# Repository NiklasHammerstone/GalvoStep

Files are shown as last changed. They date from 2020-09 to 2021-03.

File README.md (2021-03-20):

# GalvoStep
Project for building a cheap galvo laser system using Stepper motors and widely available parts.
The main goal is to engrave pictures onto wood much faster than a XY-machine could. 

This repo contains mechanical and electrical diagrams, firmware and extensive documentation of this project to maximize accessibility.
Feel free to copy/advance this project.

For a documentation of the supported G-code commands see the wiki.

### Final Update 20.03.2021

GalvoStep V1 is finished. See https://youtu.be/tV-LJvpVcUo for a typical engraving process. Accuracy is +-0.5mm I'd say. All the software can be found in CODES. 

### UPDATE 04.01.2021:
GalvoStep V1 is now functional but requires further testing. See https://youtu.be/xkFyk6ncNaY for initial test.
GUI (.py and .exe) and the Firmware for Teensy 4.0 can be found in CODES
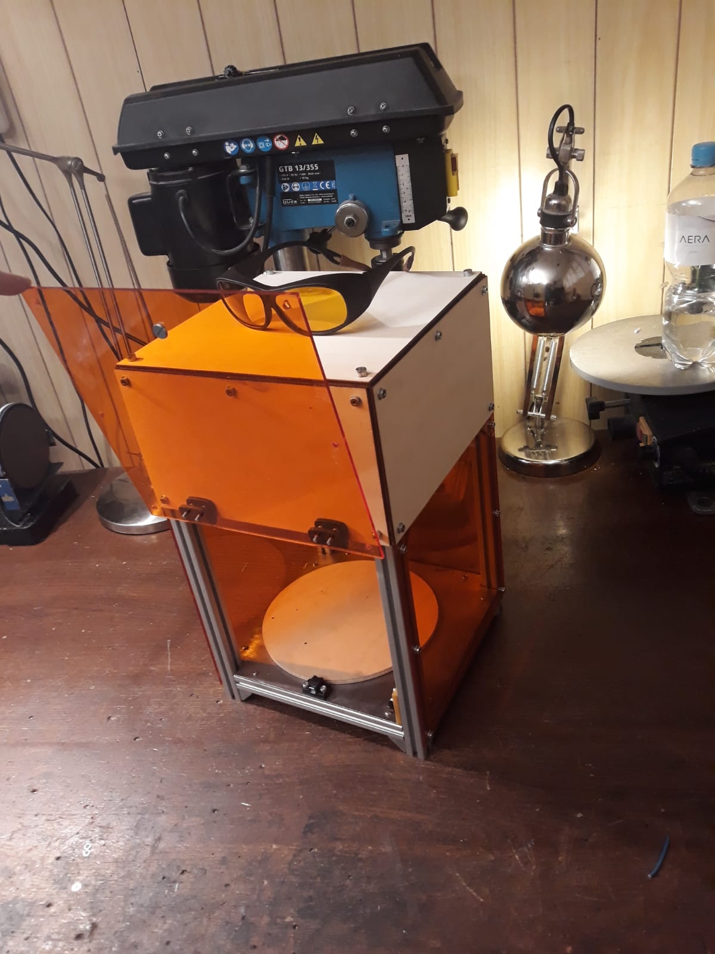
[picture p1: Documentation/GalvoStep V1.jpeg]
Most recent picture of GalvoStepV1

### UPDATE 11.10.2020:
The prototype report is done. See Documentation. GalvoStep V0 (proof-of-concept) is finished.
Now onto V1! (Goal: Actually engraving pictures)
### UPDATE 01.10.2020:
First prototype is now functional!
https://www.youtube.com/watch?v=stV5wWasxEc

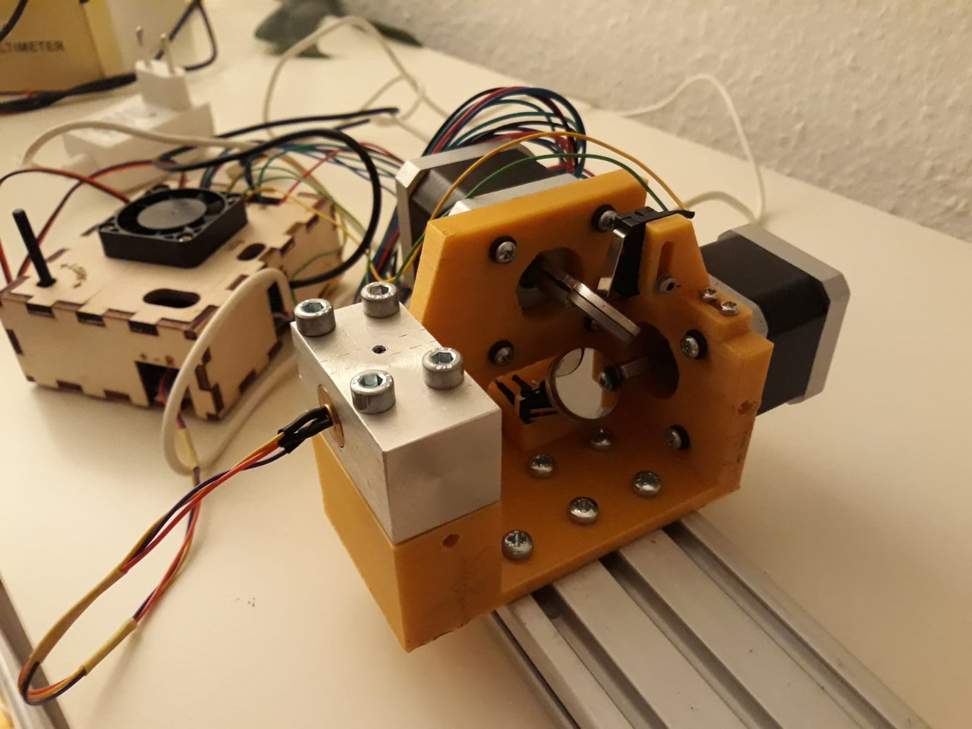
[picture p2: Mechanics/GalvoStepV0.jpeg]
Most recent picture of the prototype


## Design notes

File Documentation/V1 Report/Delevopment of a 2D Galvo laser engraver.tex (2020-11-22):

\documentclass[a4paper, 11pt]{scrartcl}
\usepackage[utf8]{inputenc}
\usepackage[english]{babel}
\usepackage[T1]{fontenc}
\usepackage{amsmath}
\usepackage{graphicx}
\usepackage{url}
\usepackage{float}
\usepackage{fancyhdr}
\bibliographystyle{plainnat}
\newcommand{\uproman}[1]{\uppercase\expandafter{\romannumeral#1}}

\title {Delevopment of a 2D Galvo laser engraver}
\author {Niklas H}
\date {\today}

\begin{document}
\maketitle
\tableofcontents
\newpage

\section{Introduction}
In this documentation, the construction of a Galvo-style high-speed laser engraver will be discussed. The goal is to upgrade the existing device to a user friendly laser engraver with high engraving speed.

\section{Theory}
In this section, relevant theory will be discussed. The development of the scanner will be based on these details. \\
\subsection{Laser diodes} 

\subsection{Stepper motors}

\subsection{Optics of the scanner} 

\section{Implementation}
In this section, construction details of the galvo scanner will be explained.
\subsection{Mechanics and Optics}
\begin{figure}[H]
\begin{center}
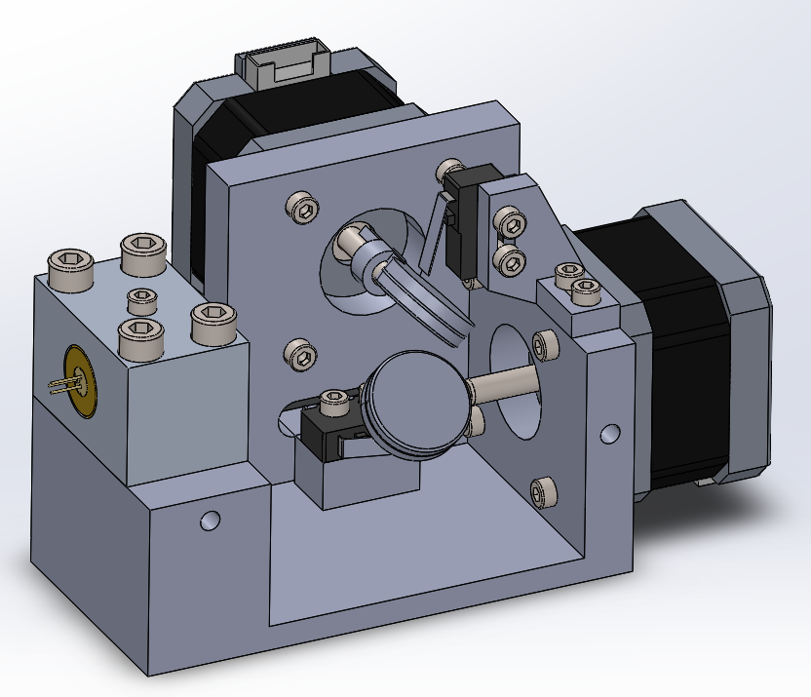
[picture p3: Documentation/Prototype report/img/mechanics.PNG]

\caption{CAD-Rendering of the mechanical system}
\label{mechanics}
\end{center}
\end{figure}

\addcontentsline{toc}{section}{References}
\bibliography{literature}
\end{document}

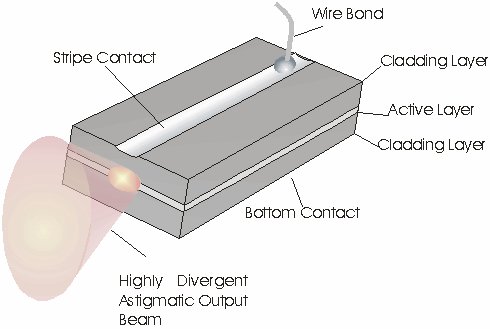
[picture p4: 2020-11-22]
Documentation/V1 Report/img/Beamshape.jpg

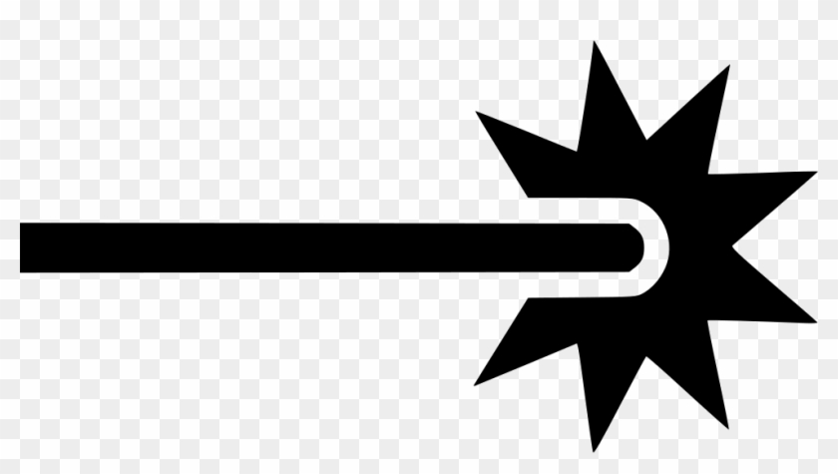
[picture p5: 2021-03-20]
Codes/lasersign.jpg

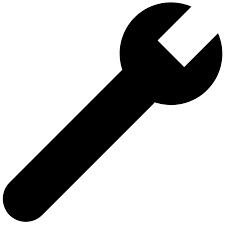
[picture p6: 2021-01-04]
Codes/wrench.png

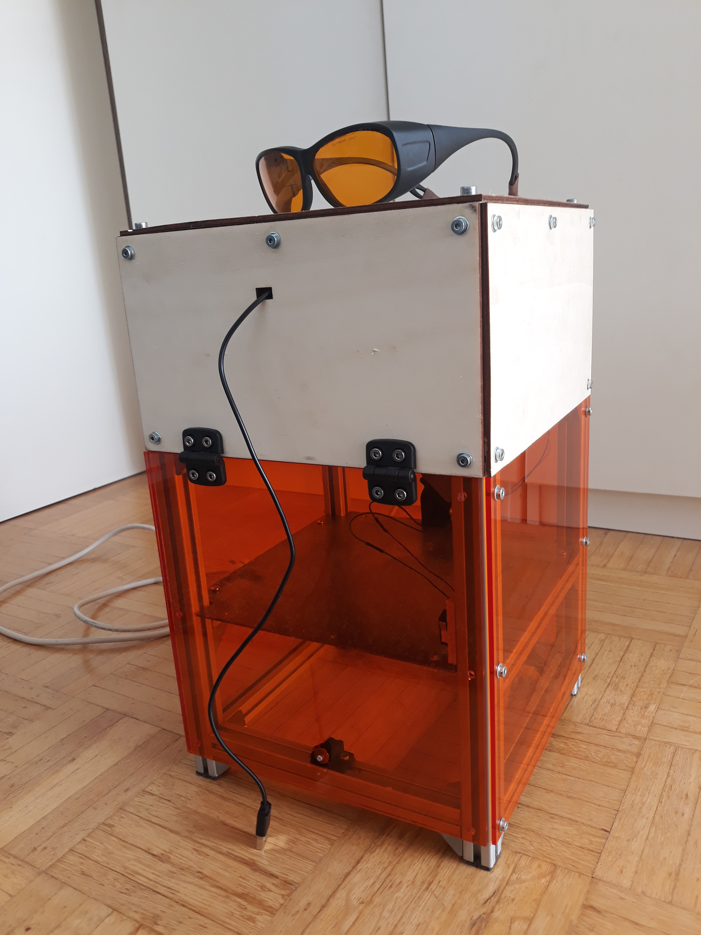
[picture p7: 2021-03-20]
Documentation/thumbnail.jpg

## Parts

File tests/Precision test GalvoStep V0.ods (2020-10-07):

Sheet: D231_F5000
 | D = 231 |  |  | F = 5000
 | TargetPosition | X | Position |  | TargetPosition | Y | Position | TargetPosition |  |  | Position
 |  |  |  |  |  |  |  | X | Y | X | Y
0 | -40 |  | -40 |  |  |  |  | 0 | 0 | 0 | 0
0 | -30 |  | -30.8 |  |  |  |  | 10 | 10 | 9.3 | 9.4
0 | -20 |  | -20.7 |  | -20 |  | -18.8 | 20 | 20 | 18.8 | 19.3
0 | -10 |  | -11.1 |  | -10 |  | -9.7 | 30 | 30 | 29.2 | 29.2
0 | 0 |  | 0 |  | 0 |  | 0 | 40 | 40 | 39.5 | 39.5
0 | 10 |  | 9 |  | 10 |  | 9.7 | 50 | 50 | 49.6 | 50
0 | 20 |  | 18.6 |  | 20 |  | 19.7 | 60 | 60 | 60.3 | 60.2
0 | 30 |  | 29.1 |  | 30 |  | 29.6 | 70 | 70
0 | 40 |  | 39.5 |  | 40 |  | 40
0 | 50 |  | 49.5 |  | 50 |  | 50
0 | 60 |  | 59.3 |  | 60 |  | 59.5
0 | 70 |  | 69.1 |  | 70 |  | 69.4
 |  |  |  |  | AVERAGE X DIFFERENCE: |  | -0.118452381 |  |  | SLOPE: | 0.999144016
 |  |  |  |  | AVERAGE Y DIFFERENCE: |  | 0.141428571 |  |  | INTERCEPT: | 0.153847409
 |  |  |  |  | MAX X DIFFERENCE: |  | 1.4
 |  |  |  |  | MAX Y DIFFERENCE: |  | 1.2

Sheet: D231_F2000
 | D = 231 |  |  | F = 2000
 | TargetPosition | X | Position |  | TargetPosition | Y | Position | TargetPosition |  |  | Position
 |  |  |  |  |  |  |  | X | Y | X | Y
0 | -40 |  | -39.5 |  |  |  |  | 0 | 0 | 0 | 0
0 | -30 |  | -29.7 |  | -30 |  | -28.7 | 10 | 10 | 9 | 10
0 | -20 |  | -19.8 |  | -20 |  | -18.6 | 20 | 20 | 18.7 | 20
0 | -10 |  | -10 |  | -10 |  | -8.5 | 30 | 30 | 29 | 30
0 | 0 |  | 0 |  | 0 |  | 0 | 40 | 40 | 39 | 40.6
0 | 5 |  | 3.8 |  | 5 |  | 5 | 50 | 50 | 49.3 | 50.7
0 | 10 |  | 8.8 |  | 10 |  | 10 | 60 | 60 | 59.1 | 61
0 | 20 |  | 18.3 |  | 20 |  | 20 | 70 | 70 | 69.5 | 71
0 | 30 |  | 28.7 |  | 30 |  | 30.3
0 | 40 |  | 38.4 |  | 40 |  | 40.6
0 | 50 |  | 48.7 |  | 50 |  | 51
0 | 60 |  | 58.6 |  | 60 |  | 60.8
0 | 70 |  | 69 |  | 70 |  | 71
0 | 80 |  | 78.6 |  | 80 |  | 81.5
 |  |  |  |  | AVERAGE X DIFFERENCE: |  | 0.003571429 |  |  | SLOPE: | 1.018746181
 |  |  |  |  | AVERAGE Y DIFFERENCE: |  | 0.155288462 |  |  | INTERCEPT: | 0.571380624
 |  |  |  |  | MAX X DIFFERENCE: |  | 1.7
 |  |  |  |  | MAX Y DIFFERENCE: |  | 1.5

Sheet: D150_F2000
 | D = 150 |  |  | F = 2000
 | TargetPosition | X | Position |  | TargetPosition | Y | Position | TargetPosition |  |  | Position
 |  |  |  |  |  |  |  | X | Y | X | Y
0 | -40 |  | -39.6 |  |  |  |  | 0 | 0 | 0 | 0
0 | -30 |  | -30.5 |  | -30 |  |  | 10 | 10 | 9 | 10
0 | -20 |  | -20 |  | -20 |  | -20.5 | 20 | 20 | 19.1 | 20
0 | -10 |  | -10 |  | -10 |  | -10 | 30 | 30 | 29.6 | 30
0 | 0 |  | 0 |  | 0 |  | 0 | 40 | 40 | 39.4 | 40
0 | 10 |  | 9.6 |  | 10 |  | 10 | 50 | 50 | 50.3 | 51
0 | 20 |  | 19.6 |  | 20 |  | 20 | 60 | 60 | 60.2 | 61.1
0 | 30 |  | 29.8 |  | 30 |  | 30.4 | 70 | 70 | 70.8 | 71.7
0 | 40 |  | 39.6 |  | 40 |  | 40.8
0 | 50 |  | 49.8 |  | 50 |  | 50.7
0 | 60 |  | 59.6 |  | 60 |  | 60.7
0 | 70 |  | 69.7 |  | 70 |  | 71.3
0 | 80 |  | 80.3 |  | 80
 |  |  |  |  | AVERAGE X DIFFERENCE: |  | 0.019230769 |  |  | SLOPE: | 1.006170769
 |  |  |  |  | AVERAGE Y DIFFERENCE: |  | -0.0675 |  |  | INTERCEPT: | 0.460257238
 |  |  |  |  | MAX X DIFFERENCE: |  | 1
 |  |  |  |  | MAX Y DIFFERENCE: |  | 1.7

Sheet: D150_F5000
 | D = 150 |  |  | F = 5000
 | TargetPosition | X | Position |  | TargetPosition | Y | Position | TargetPosition |  |  | Position
 |  |  |  |  |  |  |  | X | Y | X | Y
0 | -40 |  | -40 |  |  |  |  | 0 | 0 | 0 | 0
0 | -30 |  | -31 |  | -30 |  |  | 10 | 10 | 8.9 | 10.2
0 | -20 |  | -20.8 |  | -20 |  | -19.2 | 20 | 20 | 19.6 | 20.3
0 | -10 |  | -10.5 |  | -10 |  | -8.6 | 30 | 30 | 29.3 | 30.7
0 | 0 |  | 0 |  | 0 |  | 0 | 40 | 40 | 39.1 | 40.4
0 | 10 |  | 9.3 |  | 10 |  | 10.3 | 50 | 50 | 50 | 50.8
0 | 20 |  | 19.7 |  | 20 |  | 20.4 | 60 | 60 | 60.1 | 60.7
0 | 30 |  | 29.8 |  | 30 |  | 31 | 70 | 70
0 | 40 |  | 39.4 |  | 40 |  | 40.6
0 | 50 |  | 49.7 |  | 50 |  | 50.8
0 | 60 |  | 59.2 |  | 60 |  | 60.6
0 | 70 |  | 69.3 |  | 70 |  | 72
 |  |  |  |  | AVERAGE X DIFFERENCE: |  | -0.031547619 |  |  | SLOPE: | 1.004509858
 |  |  |  |  | AVERAGE Y DIFFERENCE: |  | 0.173571429 |  |  | INTERCEPT: | 0.738065618
 |  |  |  |  | MAX X DIFFERENCE: |  | 1.1
 |  |  |  |  | MAX Y DIFFERENCE: |  | 2
 |  |  |  |  |  |  |  |  |  |  | Trendline

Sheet: Sheet4
AVERAGE DIFFERENCE |  |  | AVERAGE DIFFERENCE
X | F2000 | F5000 | Y | F2000 | F5000
D150 | 0.019230769 | -0.031547619 | D150 | -0.0675 | 0.173571429
D231 | 0.003571429 | -0.118452381 | D231 | 0.155288462 | 0.141428571
MAXIMUM DIFFERENCE |  |  | MAXIMUM DIFFERENCE
X | F2000 | F5000 | Y | F2000 | F5000
D150 | 1 | 1.1 | D150 | 1.7 | 2
D231 | 1.7 | 1.4 | D231 | 1.5 | 1.2
SLOPE OF TRENDLINE (IDEAL LINEARITY: 1) |  |  | INTERCEPT OF TRENDLINE (IDEAL ACCURACY: 0)
 | F2000 | F5000 |  | F2000 | F5000
D150 | 1.006170769 | 1.004509858 | D150 | 0.460257238 | 0.738065618
D231 | 1.018746181 | 0.999144016 | D231 | 0.571380624 | 0.153847409

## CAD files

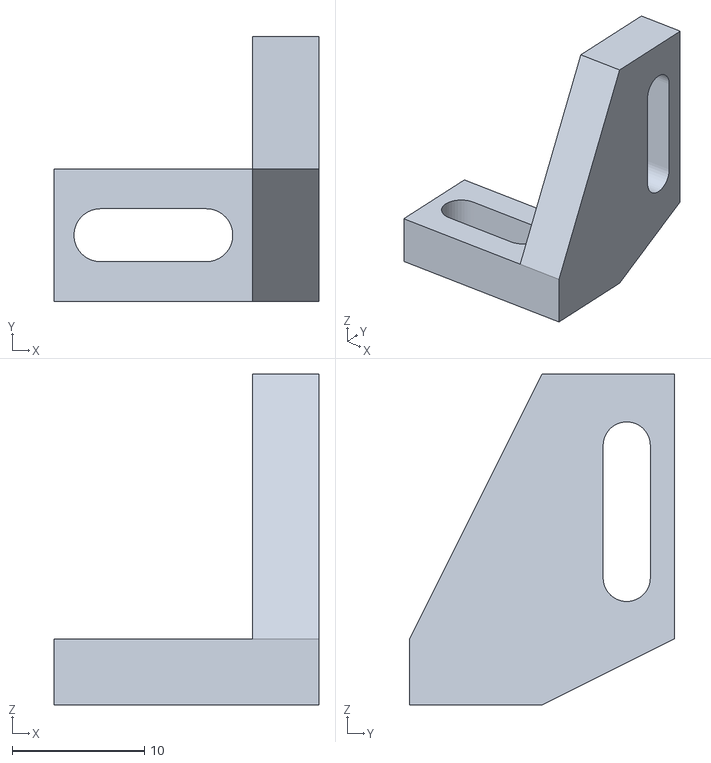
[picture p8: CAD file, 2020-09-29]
Mechanics/Endstopholder.STL
20.0 x 20.0 x 25.0

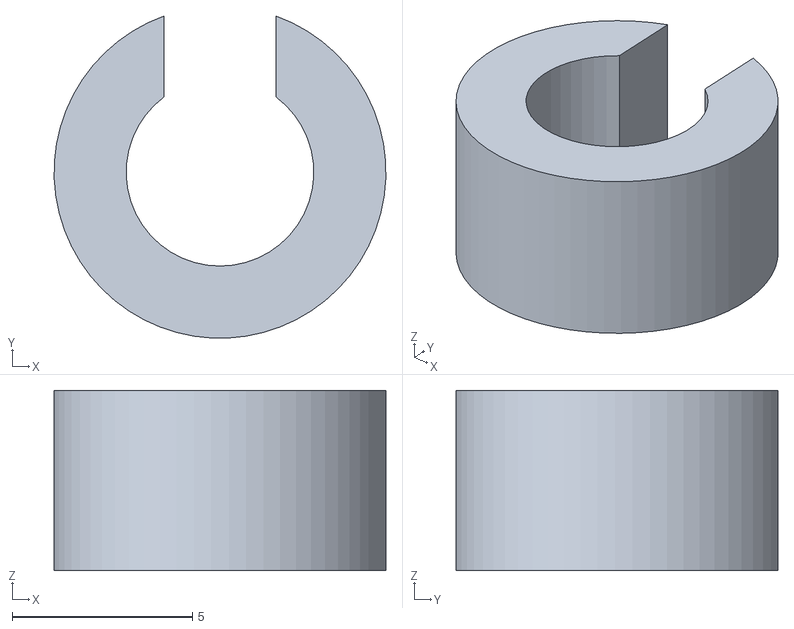
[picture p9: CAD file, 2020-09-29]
Mechanics/Holderclamp.STL
9.19 x 8.92 x 5.00

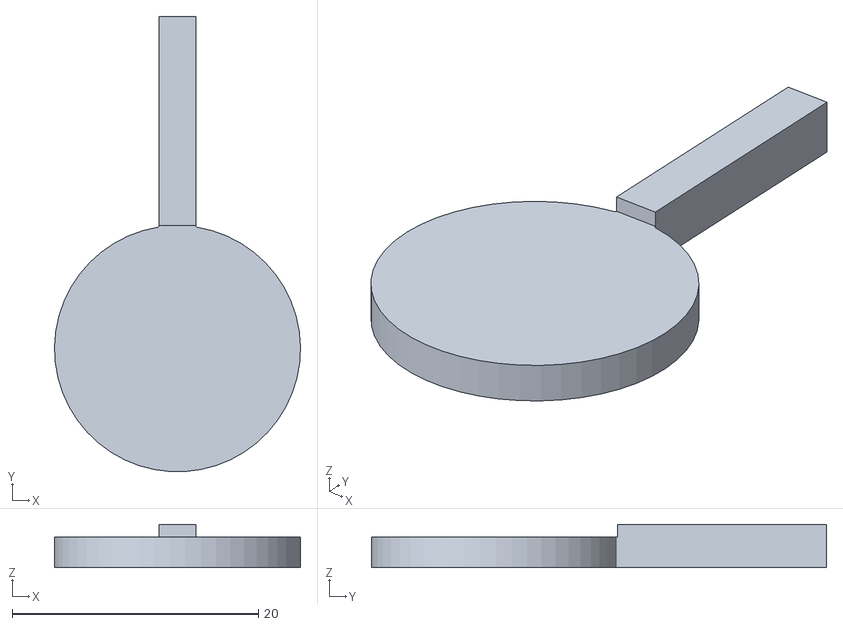
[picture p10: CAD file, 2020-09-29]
Mechanics/Mirrorholder.STL
20.0 x 37.0 x 3.50

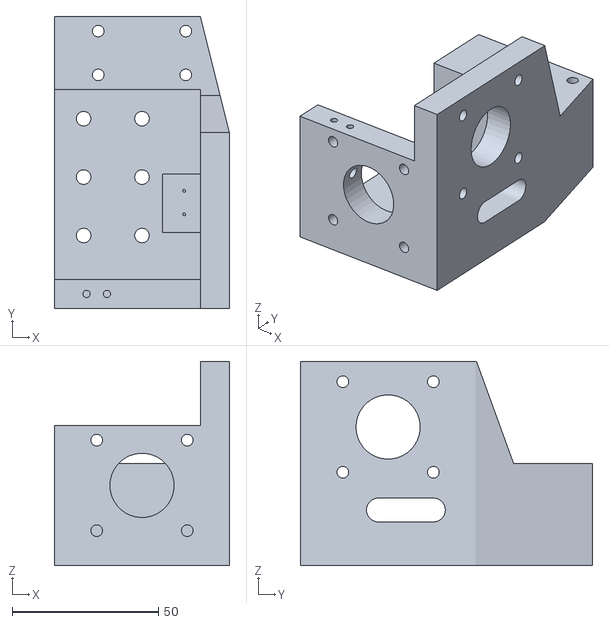
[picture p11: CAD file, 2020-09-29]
Mechanics/Base.STL
60.0 x 100.0 x 70.0

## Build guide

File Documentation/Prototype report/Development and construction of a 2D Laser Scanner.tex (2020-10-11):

\documentclass[a4paper, 11pt]{scrartcl}
\usepackage[utf8]{inputenc}
\usepackage[english]{babel}
\usepackage[T1]{fontenc}
\usepackage{amsmath}
\usepackage{graphicx}
\usepackage{url}
\usepackage{float}
\usepackage{fancyhdr}
\bibliographystyle{plainnat}
\newcommand{\uproman}[1]{\uppercase\expandafter{\romannumeral#1}}

\title {Development and construction of a 2D Laser Scanner}
\author {Niklas H}
\date {\today}

\begin{document}
\maketitle
\tableofcontents
\newpage
\section{Introduction}
Many laser scanning\footnote{The term scanning in this context refers to material processing (e.g. engraving) line-by-line} systems for material processing today are based on galvanometer-actuated mirror systems and utilize fiber lasers ($\lambda = 1064nm$) for efficient and fast engraving on metals. However, galvanometers are expensive and complicated to drive.  This projects goal is to create a similar system using stepper motors, which are very simple to use and laser diodes ($\lambda=650nm$ and $\lambda=445nm$). The secondary goal is to create a cheap but accurate drive system which should be possible to build with minimal tools (3D-Printer, lathe (optional) and basic soldering equipment) from scratch. For this sake, two versions will be built, the first one utilizing a low power laser diode and no f-theta lens for a safe proof-of-concept and the second one utilizing a high-power laser diode for engraving. \\
In this documentation, the mechanical, electrical, mathematical and programming side of the first project will be discussed.

\section{Theory}
In this section, relevant theory will be discussed. The development of the scanner will be based on these details. \\
\subsection{Laser diodes} 
Laser diodes are special semiconductors that emit spatially coherent and monochromatic light of a specific wavelength $\lambda$ (laser beam). Laser diodes are relatively fragile components which electrically behave similar to normal diodes, meaning low resistance in one current direction and high resistance in the opposite direction. For laser diodes to work properly, they must be driven with a constant current\footnote{Laser diodes are easily damaged by current spikes or excess heat}. Therefore, it is good practice to use constant current sources and heatsinks for driving laserdiodes. Also, laser diodes oftentimes emit laser beams with relatively high divergence, so an optical collimator is required in order to reduce the divergence to a few $mrad$. 

\subsection{Stepper motors}
Stepper motors reach high positioning accuracy by performing movements in discrete steps (usually $1.8^\circ$). The appropriate winding currents are supplied by stepper motor drivers. These drivers are given two signals: STEP and DIR. One STEP pulse from the controller advances the motor position one step, whilst the DIR signal (low or high) indicates the direction. The accuracy can be improved by using special drivers which interpolate the rotation between poles (micro-stepping). 

\subsection{Optics of the scanner} 
\begin{figure}[H]
\begin{center}
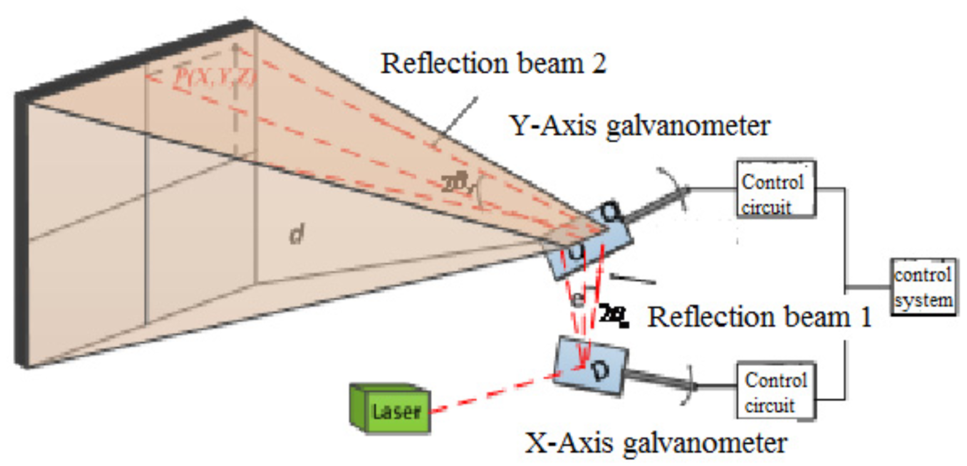
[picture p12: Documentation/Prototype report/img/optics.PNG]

\caption{Model of the optical mirror system \cite{Meng.2019}}
\label{optics}
\end{center}
\end{figure}
Because the scanner can only indirectly control the laser dot on the working plane by turning its mirrors, some sort of mathematical representation of this system must be derived. This representation will used for turning XY-directions into mirror rotation angles. From \cite{Meng.2019} we get the following equations:
\begin{equation}\label{eqn1}
x=e\cdot tan(2\theta_x)+tan(2\theta_x) \cdot \sqrt{d^2+y^2} 
\end{equation} 
\begin{equation}\label{eqn2}
y = d\cdot tan(\theta_y)
\end{equation} 
where $x$ and $y$ are the point coordinates on the plane, $\theta_x$ and $\theta_y$ are the rotations angles of the mirrors\footnote{More specifically: $\theta_x$ is the angle between the laser beam and the first reflection beam minus $90^\circ$. Similarly, $\theta_y$ is the angle between the first and second reflection beam minus $90^\circ$.}, $e$ is the vertical distance between the mirror axes and $d$ is the normal distance between the projection plane and the Y-mirror rotation axis. \\
Since $x$ and $y$ are given by the user (rather the gcode), equations \ref{eqn1} and \ref{eqn2} must be solved for $\theta_x$ and $\theta_y$. These angles will be turned into step signals for the steppers. From equation \ref{eqn2} we can derive 
\begin{equation}\label{eqn3}
\theta_y = \frac{arctan(\frac{y}{d})}{2}
\end{equation} 
From equation \ref{eqn1}, $\theta_x$ can be found:
\begin{equation}\label{eqn4}
\theta_x=\frac{arctan\left( \frac{x}{e+\sqrt{d^2+y^2}}\right) }{2}
\end{equation}
Looking at figure \ref{optics}, $x$ and $y$ must be zero, when $\theta_x=\theta_y=0^\circ$ \footnote{with these angles, all beams are orthogonal. This configuration is referred to the neutral or home position.}. Equations \ref{eqn3} and \ref{eqn4} confirm this. 

\section{Implementation}
In this section, construction details of the galvo scanner will be explained.
\subsection{Mechanics and Optics}
\begin{figure}[H]
\begin{center}

\caption{CAD-Rendering of the mechanical system}
\label{mechanics}
\end{center}
\end{figure}
The mechanics of this design are relatively simple: The mirrors are attached to stepper motors by glueing aluminium holders onto the flat piece of the rotor and glueing the mirrors (in this case 20x3mm molybdenum mirrors) onto the holder and the rotor\footnote{The holders were machined and 3D-printed (PLA, 100\% infill) to test the difference in performance, but none was noticeable. The molybdenum mirrors are relatively heavy, but are the cheapest viable option available.}. The motors are then screwed onto the 3D-printed base (PLA, 60\% infill). This base also has features to screw on endswitches (for homing the mirrors) and the laserdiode array. The latter consists of a machined aluminium block into which the laserdiode holder (machined brass) fits. This holder also has a M9x0.5 thread for the collimator unit. The collimator can be adjusted via this thread. \\
\subsection{Electronics}
\begin{figure}[H]
\begin{center}
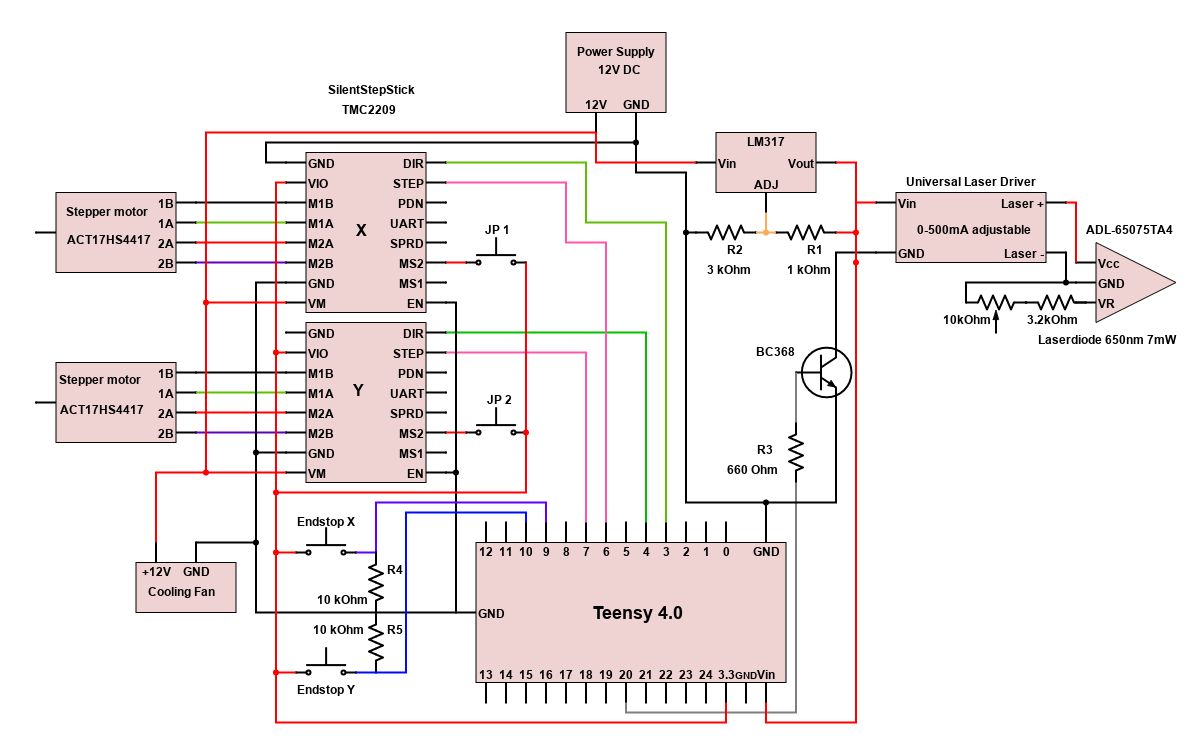
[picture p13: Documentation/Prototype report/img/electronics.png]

\caption{Wiring diagram for the system}
\label{electronics}
\end{center}
\end{figure}
Figure \ref{electronics} shows the electrical diagram of the system. The stepper motors are Nema-17 ACT 17hs4417 steppers. The SilentStepSticks (containing Trinamic TMC2209 ICs)  were chosen as drivers because of their high micro-stepping capabilities (up to 256), extremely low noise and relatively low cost (about 10 Euros or 12 USD per driver). \\
For the main controller, a Teensy 4.0 was chosen because of the extremely high clock frequency of 600Mhz\footnote{In comparison, an Arduino Nano only has 16MHz clock frequency!} and its easy programmability through the Arduino IDE. It must be noted, that the Teensy 4.0 only tolerates 3.3V logic voltage. 

\paragraph{Note:} Teensy Boards and laserdiodes can be very fragile electrical components (multiple Teensies and Diodes were destroyed in this project), so it may be worth the money and effort to use an Arduino in order to test the circuits/code and use dummy loads for simulating laser diodes. Since the SilentStepStick-Drivers can tolerate 3.3V and 5V as logic voltages, the microcontrollers can be changed without changing the circuit. However, the footprints are not equal, so jumper cables are necessary for replacing the Teensy with an Arduino. \\

For driving the laserdiode, a special diode driver is used, which can supply 0-500mA of constant regulated current\footnote{It is possible to use a LM317 and correct resistors for a constant current source. This was tested in this project, but resulted in a lot of destroyed laser diodes, which is why a complete driver circuit was bought.}. \\
This driver circuit is activated by a NPN-Transistor (specifially, a BC368). For calculating its base resistance $R_2$, a base current of the BC368 transistor of $I_B=5mA$ is selected \cite[p. 3]{SemiconductorComponentsIndustries.2007}. Since the Teensy 4.0 logic voltage is $3.3V$, a resistance value of $R_2=\frac{3.3V}{5mA}=660\Omega$ is selected. \\
The laser diode has three pins: \textit{Vcc}, \textit{GND} and \textit{VR}. \textit{Vcc} is connected to the output of the constant current source, \textit{GND} is connected to the \textit{Laser -} pin of the diode driver. \textit{VR} is connected to \textit{Laser -} via a resistance of $3k\Omega$ (maximum power) - $13k\Omega$ (minimum power), which is realised with fixed resistors ($3.2k\Omega$) in series with a linear potentiometer ($10k\Omega$). The GND of the diode driver is connected to a transistor to switch it on or off.\\
For supplying Vcc (5V) for the Teensy and the laser driver, a LM317 linear voltage regulator is used in the shown configuration. The resistors $R_1$ and $R_2$ can be computed as follows \cite[p. 10]{lm317}: 
\begin{equation}
V_{out} = 1.25 \cdot \left( 1+\frac{R_2}{R_1} \right)
\end{equation}
$V_{out}$ must be 5V and $R_1$ is chosen to be $1k\Omega$. Therefore, $R_2$ must be:
\begin{equation}
R_2 = \left( \frac{V_{out}}{1.25V} - 1 \right) \cdot R_1 =  \left( \frac{5V}{1.25V} - 1 \right) \cdot 1000\Omega = 3000\Omega
\end{equation}
$R_4$ and $R_5$ are pull-down resistors that draw the pin state of pins $9$ and $10$ (pins for the endstops) to the low state to prevent undefined behaviour. \\
$JP_1$ and $JP_2$ are jumpers that set the microstepping mode of the stepper motor drivers to $\frac{1}{8}$ (jumper disconnected) or $\frac{1}{64}$ (jumper connected).
\subsection{Code}
\begin{figure}[H]
\begin{center}
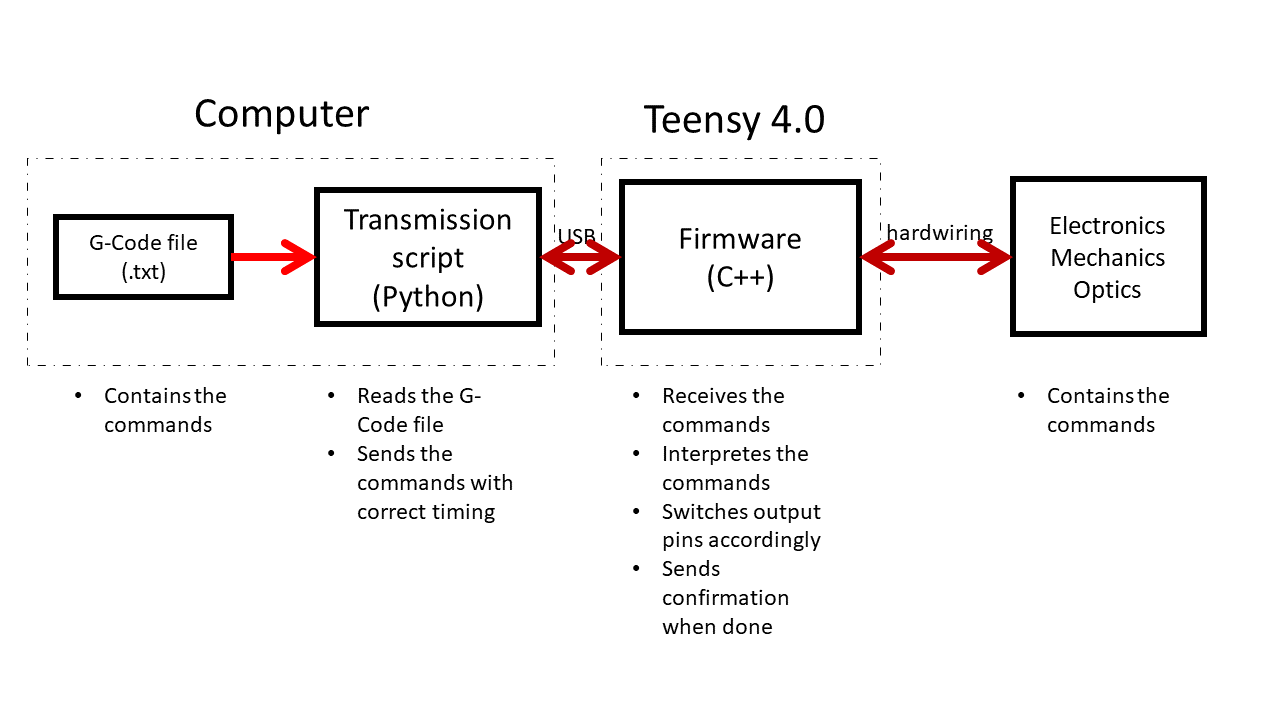
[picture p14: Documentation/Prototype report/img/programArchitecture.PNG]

\caption{A simplified diagram of the program architecture}
\label{code}
\end{center}
\end{figure}
The programm architecture (see figure \ref{code}) consists of three main parts: The teensy firmware, a python script for Gcode transmission and the G-Code itself. 
\paragraph{Firmware}
The firmware is the most critical part of the architecture: It interpretes the received (via Serial) G-Code commands and coordinates all of the outputs and inputs, such as step and direction signals and the transistor base for the laser or the endstop signals. Because it is directly compiled onto the Teensy via the Arduino IDE, it is written in C++.\\
The firmware supports the following G-Code commands: G0, G1, G2, G3, G28, G60, G61, M3, M4, M5, M201, M203. \footnote{For a detailled explanation and syntax details, see the GalvoStep wiki at \url{https://github.com/NiklasHammerstone/GalvoStep}} The firmware sends a short confirmation (usually: \textit{OK}), when the command is processed. If it included stepper movement (such as G0), the confirmation will only be sent when steppers have reached their target position.
\paragraph{Transmission script}
The transmission script is a Python script that reads the G-Code file from a specified location on the PC. The gcode is read, encoded and sent via a Serial connection (USB). Before the next line is sent, the script waits for a confirmation from the firmware. This makes sure that no command is sent before the firmware is finished processing the previous command. This loop is repeated until no G-Code commands are left to send.
\paragraph{G-Code}
The G-Code file is a simple text file (.txt) which contains the command lines. It is critical that each line only contains one command. \\

\section{Results}
\subsection{General functionality}
The proposed functionality was realised. The prototype can be given commands by sending G-Code commands via the Arduino IDE Serial Monitor or a Python script\footnote{The code files can be downloaded via GitHub: \url{https://github.com/NiklasHammerstone/GalvoStep}}. The commands are executed instantly. No delay between commands is perceivable when a whole G-Code file is executed via the Python script. This results in a smooth movement of the laser spot. \\
A G-Code file drawing a heart shape was tested with step frequencies of $2000 \frac{steps}{s}$ up to $20000\frac{steps}{s}$ and a distance from the projection plane of about $200mm$. At about $10000-12000 \frac{steps}{s}$ the moving spot started to look like a (more or less) stationary image\footnote{This is only true for the naked eye. Also, the border step frequency is dependent on the size of the image, the background, the laser intensity and the general lighting of the room.}, with the shape of the image still not being noticeably distorted. At about $15000-18000 \frac{steps}{s}$ the image stationarity was satisfactory, but mechanical vibrations led to a distorted image. The results of this test can be seen in figures \ref{slow} and \ref{fast}. 
\begin{figure}[!h]
\noindent
\begin{minipage}{0.4\textwidth}%
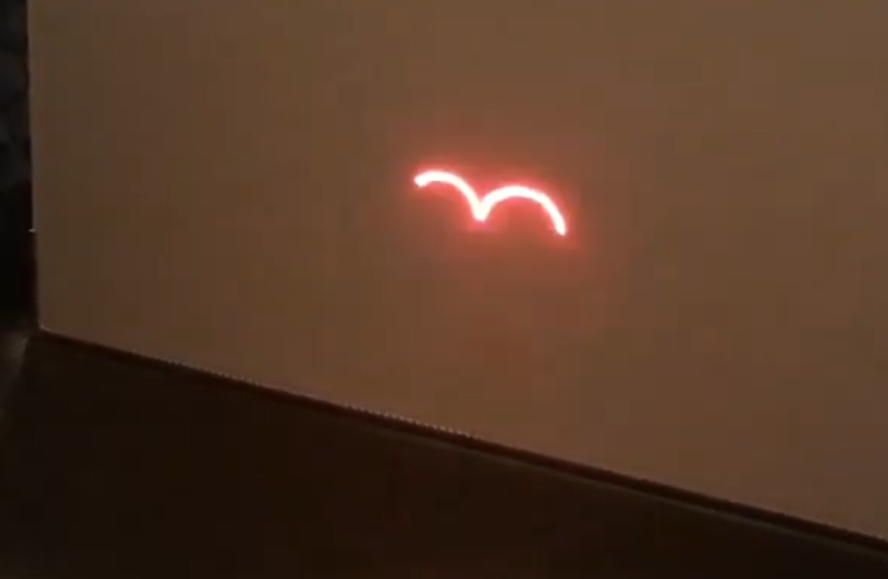
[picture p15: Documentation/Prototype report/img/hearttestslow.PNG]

\caption{Arcs of the projected heart at $8000 \frac{steps}{s}$}
\label{slow}
\end{minipage}%
\hfill
\begin{minipage}{0.4\textwidth}%
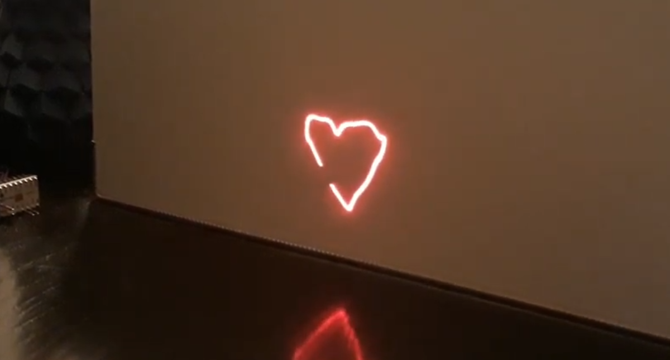
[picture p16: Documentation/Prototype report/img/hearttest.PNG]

\caption{Almost entire heart at $20000 \frac{steps}{s}$}
\label{fast}
\end{minipage}%
\end{figure}
Note that the rolling shutter of the camera is quite fast, which is why only the picture at about $20000 \frac{steps}{s}$ is (almost) completely visible in one photo. However the difference of the arcs alone should convey the diffence of the whole picture. \\
\subsection{Accuracy and precision}
\begin{figure}[H]
\begin{center}
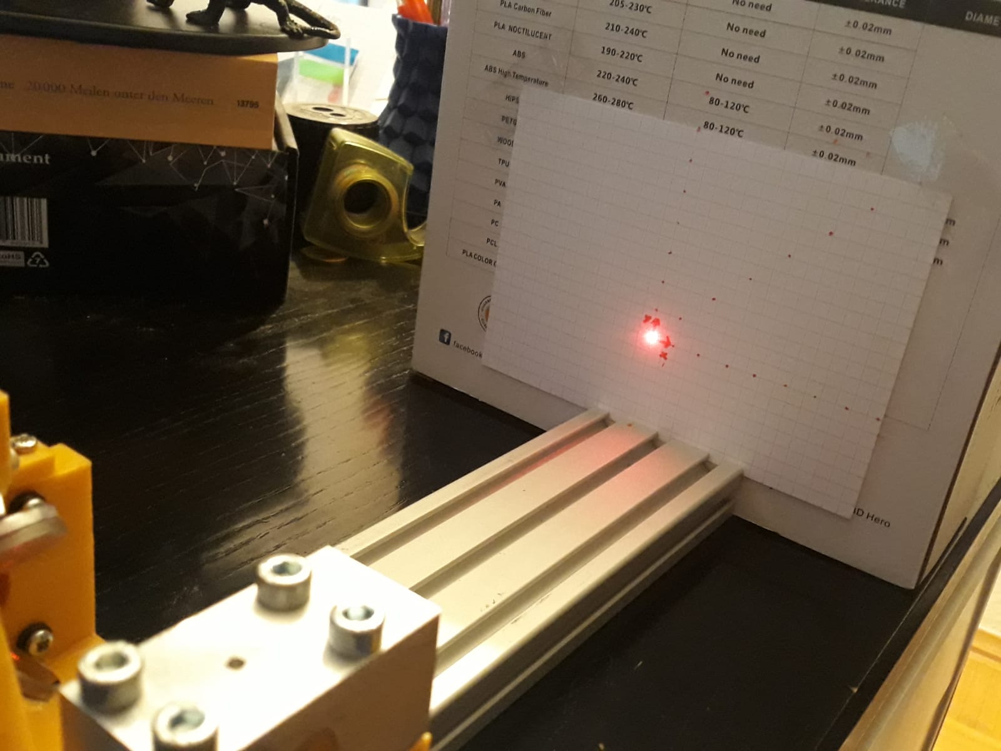
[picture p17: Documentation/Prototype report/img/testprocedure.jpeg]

\caption{Snapshot of the testing procedure}
\label{testing}
\end{center}
\end{figure}
In order to test the accuracy of the prototype, the following procedure was performed:
\begin{enumerate}
\item Place the machine in front of a plane with a defined distance D.
\item Home the mirrors.
\item Move the laser point in 10mm steps in X-, Y-, and XY direction (from -20 to +80) with speed F.\footnote{An example command for testing the XY direction would be \textit{G0 X20 Y20}. In this test, X and Y coordinates were always equal to reach an ideal line of slope 1.}
\item Mark the actual laser spot carefully with a pen for each step (see figure \ref{testing})\footnote{Since the prototype utilizes a 7mW laser diode, the laser itself is too weak to mark the paper by itself.}
\item After the testing is done, measure the actual distances of the spots from the origin point.
\end{enumerate}
From the Y-, X- and XY, the average and maximum difference from the ideal coordinates are computed. For the XY-coordinates, average slope and intercept were calculated to analyze the linearity of the system.
\begin{figure}[H]
\begin{center}
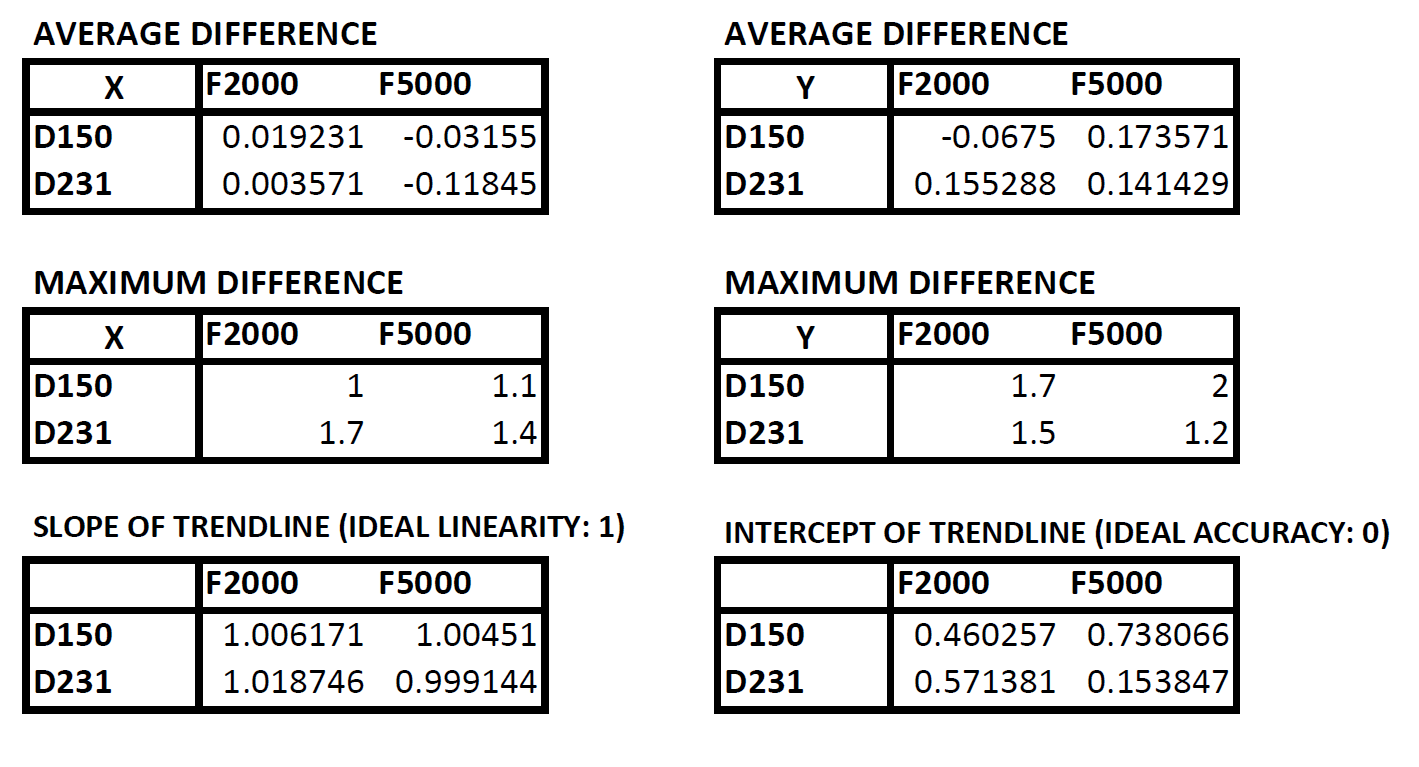
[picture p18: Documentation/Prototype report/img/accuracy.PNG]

\caption{Results of the accuracy analysis}
\label{results}
\end{center}
\end{figure}
In figure \ref{results} the results of the mentioned tests are shown. It is expected, that the average and maximum differences (representing positional accuracy) would rise with rising distance \textit{D} and feedrate \textit{F}. However, no such trends can be seen from the data. The average difference is consistently lower than $0.2mm$, but the absolute maximum is $2mm$. This suggests relatively high accuracy, but low precision. This is verified by the slope of the trendline for the XY-point testing. The highest difference from the ideal slope of 1 (since the same values were used for X and Y coordinates simultaneously) was $0.018\frac{mm}{mm}$, suggesting high accuracy. However, the intercepts of the trendlines (ideal would be zero) differ widely from zero, with differences going as high as $0.738mm$, suggesting low precision. This result suggests that the machine is working correctly\footnote{\glqq Working correctly\grqq refers to the mathematic model being correct and the physical, electrical and optical design being expedient in theory}, but is lacking the mechanical alignment for high precision.\\ 
Furthermore, the repeatability of the endstops and backlash of the motors was tested. For the repeatability test of the endstops, the machine was homed ten times (homing speed: $500\frac{steps}{s}$) and the spot offsets were noted. The average difference was about $0.3mm$ with a maximum of $2mm$, resulting in a arc accuracy of $0.5^\circ$. These inaccuracies are most likely due to the cheap mechanical endstops used.\\
For the backlash test, the machined was homed and the spot was moved by $80mm$ back and forth multiple times in X and Y directions. As expected (because no parts are present that could induce backlash), no backlash was perceivable.
\subsection{Flaws of the testing methodology} It must be noted that the proposed method of testing has inherent inaccuracies: Since the laser can not mark paper by itself, it is necessary to use a pen, but as soon as the pen is brought into position, it blocks the laser beam. This way its necessary for the operator to visually remember where the spot was. The marked spot can be checked by removing the pen and therefore unblocking the pen, but since both the spot and the pen marking have a diameter of approximately $1.5mm$\footnote{The actual laser spot is much smaller than this, but appears to be larger due the light  being scattered and dispersed in the surrounding paper}, this method can not guarantee results within about half of that range ($0.5 - 0.9 mm$). This can be partly compensated by making sure that the caliper blades are positioned in the exact middle (which itself is only possible within a few tenths of a millimeter) of the pen marking when measuring the points. Also, the paper pieces used for this test did bow out by approximately $1mm$, which is unideal. In conclusion, the difference of laser spot and pen marking and the measuring inaccuracies add up to such a big margin of error (approximately $\pm 1mm$) that the exact values of the point coordinates are relatively useless for accuracy analysis. However, since the presented flaws are unsystematic and randomn (except for the bow of the paper), the averages (average distance, slope and intercept of trendline) should be more conclusive. \\
These flaws can be elimininated entirely by using a more powerful laser which can mark wood by itself. This would eliminate the pen method with all its flaws and inaccuracies and only leave the direct measuring inaccuracies of the calipers, which are usually within $0.02 - 0.1mm$. \\

\section{Conclusion}
In conclusion, the goal of a proof-of-concept for a steppermotor-actuated galvoprojector was reached. The machine can be used via G-Code like a normal CNC-machine (e.g. 3D-printer, CNC-Router) and can draw figures with step speeds of up to $20000 \frac{steps}{s}$, depending on how much distortion is acceptable for the user. Since this machine cannot compete with laser projectors using real galvoactuators, its most probable usecase would be engraving with speeds unreachable for most CO2 or diode daser machines currently on the market. Since the precision of the current prototype is quite limited (as shown in the chaper Results), more work is required to be able compete with normal benchtop laser engravers (see Prospect).
\section{Prospect}
In the following versions of this machine, the steppermotors and endstops will be upgraded. The base will be re-designed to fit the new high-power laser module and the mirrors will be replaced. An F-theta objective might be added to increase light intensity at the working plane and therefore engraving speed. Finally, safety precautions (Enclosure with laser windows and doorswitch) will be added to shield the laser beam. The electronics will not be changed much, since they worked without problems\footnote{Maybe a PCB will be designed and manufactured for the schematic.}. 
\section{Acknowledgements}
Special thanks to the members of the forum \url{www.laser-engravers.de}, especially \glqq VDX \grqq and \glqq Gewindestange\grqq, without which a lot more laser diodes would have been destroyed in the process of this project.

\addcontentsline{toc}{section}{References}
\bibliography{literature}
\end{document}

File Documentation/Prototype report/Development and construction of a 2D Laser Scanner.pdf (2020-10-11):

# Development and construction of a 2D Laser Scanner

## Niklas H

## October 11, 2020

## Contents

1 Introduction | 2
2 Theory | 2
3 Implementation | 4
4 Results | 8
5 Conclusion | 11
6 Prospect | 12
7 Acknowledgements | 12
References | 12

1

## 1 Introduction

Many laser scanning¹
systems for material processing today are based on galvanometeractuated mirror systems and utilize ber lasers (λ = 1064nm) for ecient and fast engraving on metals. However, galvanometers are expensive and complicated to drive. This projects goal is to create a similar system using stepper motors, which are very simple to use and laser diodes (λ = 650nm and λ = 445nm). The secondary goal is to create a cheap but accurate drive system which should be possible to build with minimal tools (3D-Printer, lathe (optional) and basic soldering equipment) from scratch. For this sake, two versions will be built, the rst one utilizing a low power laser diode and no f-theta lens for a safe proof-of-concept and the second one utilizing a high-power laser diode for engraving.
In this documentation, the mechanical, electrical, mathematical and programming side of the rst project will be discussed.

## 2 Theory

In this section, relevant theory will be discussed. The development of the scanner will be based on these details.

2.1 Laser diodes

Laser diodes are special semiconductors that emit spatially coherent and monochromatic light of a specic wavelength λ (laser beam). Laser diodes are relatively fragile components which electrically behave similar to normal diodes, meaning low resistance in one current direction and high resistance in the opposite direction. For laser diodes to work properly, they must be driven with a constant current²
. Therefore, it is good practice to use constant current sources and heatsinks for driving laserdiodes. Also, laser diodes oftentimes emit laser beams with relatively high divergence, so an optical collimator is required in order to reduce the divergence to a few mrad.

2.2 Stepper motors

Stepper motors reach high positioning accuracy by performing movements in discrete steps (usually 1.8

◦
). The appropriate winding currents are supplied by stepper motor drivers. These drivers are given two signals: STEP and DIR. One STEP pulse from the controller advances the motor position one step, whilst the DIR signal (low or high) indicates the direction. The accuracy can be improved by using special drivers which interpolate the rotation between poles (micro-stepping).

1The term scanning in this context refers to material processing (e.g. engraving) line-by-line 2Laser diodes are easily damaged by current spikes or excess heat

2

2.3 Optics of the scanner

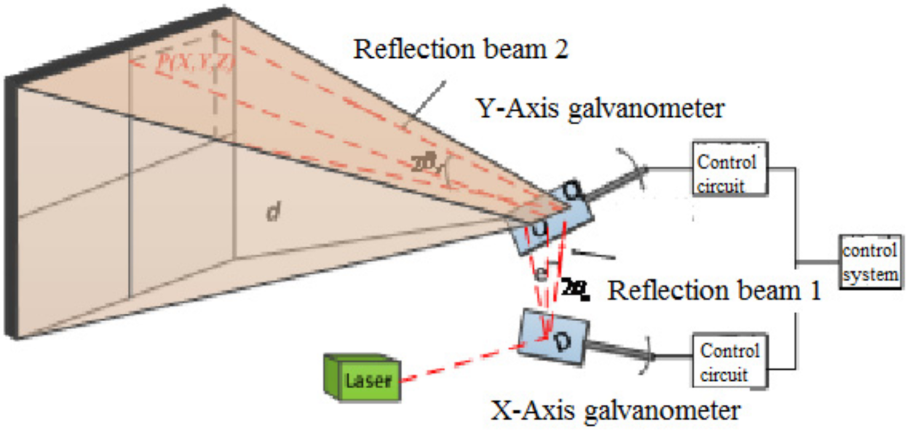
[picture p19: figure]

Figure 1: Model of the optical mirror system [Meng et al.(2019)Meng, Cao, Li, and Lv]

Because the scanner can only indirectly control the laser dot on the working plane by turning its mirrors, some sort of mathematical representation of this system must be derived. This representation will used for turning XY-directions into mirror rotation angles. From [Meng et al.(2019)Meng, Cao, Li, and Lv] we get the following equations:

x = e · tan(2θx) + tan(2θx) ·

p
d

2 + y

2 | (1)
y = d · tan(θy) | (2)

where x and y are the point coordinates on the plane, θx and θy are the rotations angles of the mirrors³
, e is the vertical distance between the mirror axes and d is the normal distance between the projection plane and the Y-mirror rotation axis.
Since x and y are given by the user (rather the gcode), equations 1 and 2 must be solved for θx and θy. These angles will be turned into step signals for the steppers. From equation 2 we can derive

θy =

arctan(

y
d

)
2 | (3)

From equation 1, θx can be found:

θx =

arctan
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
3More specically: θx is the angle between the laser beam and the rst reection beam minus 90◦ .
Similarly, θy is the angle between the rst and second reection beam minus 90◦

3

Looking at gure 1, x and y must be zero, when θx = θy = 0◦ 4 . Equations 3 and 4
conrm this.

## 3 Implementation

In this section, construction details of the galvo scanner will be explained.

3.1 Mechanics and Optics


Figure 2: CAD-Rendering of the mechanical system

4with these angles, all beams are orthogonal. This conguration is referred to the neutral or home position.

4

The mechanics of this design are relatively simple: The mirrors are attached to stepper motors by glueing aluminium holders onto the at piece of the rotor and glueing the mirrors (in this case 20x3mm molybdenum mirrors) onto the holder and the rotor⁵
. The
motors are then screwed onto the 3D-printed base (PLA, 60% inll). This base also has features to screw on endswitches (for homing the mirrors) and the laserdiode array. The latter consists of a machined aluminium block into which the laserdiode holder (machined brass) ts. This holder also has a M9x0.5 thread for the collimator unit. The collimator can be adjusted via this thread.

3.2 Electronics

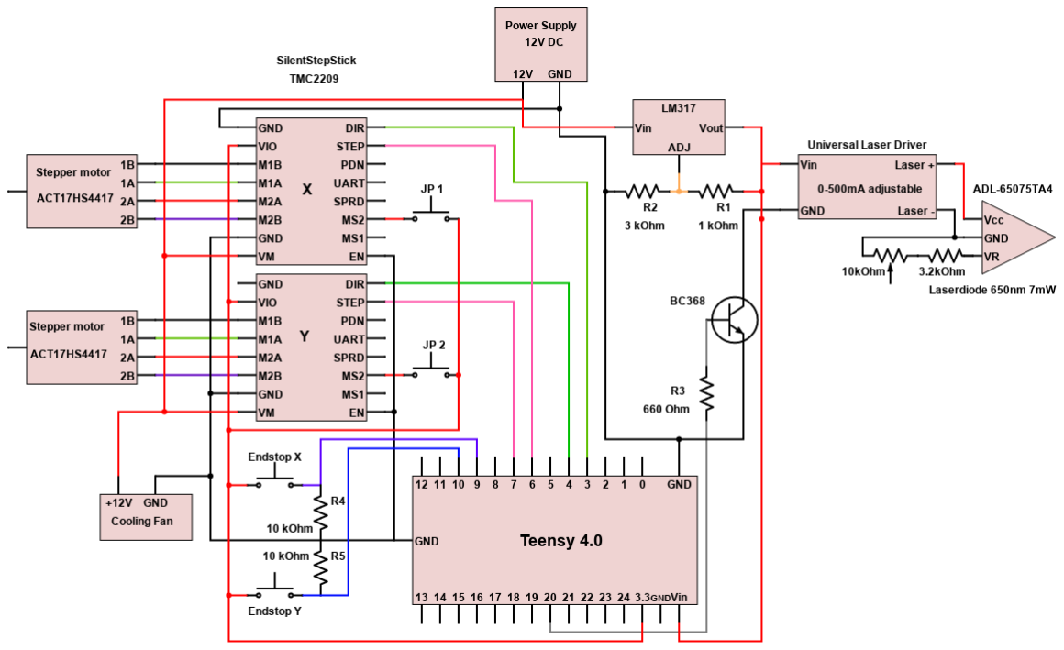
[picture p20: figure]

Figure 3: Wiring diagram for the system

Figure 3 shows the electrical diagram of the system. The stepper motors are Nema-17 ACT 17hs4417 steppers. The SilentStepSticks (containing Trinamic TMC2209 ICs) were chosen as drivers because of their high micro-stepping capabilities (up to 256), extremely low noise and relatively low cost (about 10 Euros or 12 USD per driver).
For the main controller, a Teensy 4.0 was chosen because of the extremely high clock

5The holders were machined and 3D-printed (PLA, 100% inll) to test the dierence in performance, but none was noticeable. The molybdenum mirrors are relatively heavy, but are the cheapest viable option available.

5

frequency of 600Mhz⁶ and its easy programmability through the Arduino IDE. It must be noted, that the Teensy 4.0 only tolerates 3.3V logic voltage.

Note: Teensy Boards and laserdiodes can be very fragile electrical components (multiple Teensies and Diodes were destroyed in this project), so it may be worth the money and eort to use an Arduino in order to test the circuits/code and use dummy loads for simulating laser diodes. Since the SilentStepStick-Drivers can tolerate 3.3V and 5V as logic voltages, the microcontrollers can be changed without changing the circuit. However, the footprints are not equal, so jumper cables are necessary for replacing the Teensy with an Arduino.

For driving the laserdiode, a special diode driver is used, which can supply 0-500mA of constant regulated current⁷
This driver circuit is activated by a NPN-Transistor (specially, a BC368). For calculating its base resistance R2, a base current of the BC368 transistor of IB = 5mA is selected [Sem(2007), p. 3]. Since the Teensy 4.0 logic voltage is 3.3V , a resistance value of R2 =

3.3V
5mA = 660Ω is selected.
The laser diode has three pins: Vcc, GND and VR. Vcc is connected to the output of the constant current source, GND is connected to the Laser - pin of the diode driver. VR is connected to Laser - via a resistance of 3kΩ (maximum power) - 13kΩ (minimum power), which is realised with xed resistors (3.2kΩ) in series with a linear potentiometer (10kΩ). The GND of the diode driver is connected to a transistor to switch it on or o. For supplying Vcc (5V) for the Teensy and the laser driver, a LM317 linear voltage regulator is used in the shown conguration. The resistors R1 and R2 can be computed as follows [lm3(2014), p. 10]:

Vout = 1.25 ·

1 +

R2
R1
(5)

Vout must be 5V and R1 is chosen to be 1kΩ. Therefore, R2 must be:

R2 =

Vout
1.25V

− 1

- R1 =
5V
1.25V

− 1

- 1000Ω = 3000Ω | (6)

R4 and R5 are pull-down resistors that draw the pin state of pins 9 and 10 (pins for the endstops) to the low state to prevent undened behaviour.
JP1 and JP2 are jumpers that set the microstepping mode of the stepper motor drivers to 1
8

(jumper disconnected) or 1
64 (jumper connected).

6
In comparison, an Arduino Nano only has 16MHz clock frequency!

7
It is possible to use a LM317 and correct resistors for a constant current source. This was tested in this project, but resulted in a lot of destroyed laser diodes, which is why a complete driver circuit was bought.

6

3.3 Code


Figure 4: A simplied diagram of the program architecture

The programm architecture (see gure 4) consists of three main parts: The teensy rmware, a python script for Gcode transmission and the G-Code itself.

Firmware The rmware is the most critical part of the architecture: It interpretes the received (via Serial) G-Code commands and coordinates all of the outputs and inputs, such as step and direction signals and the transistor base for the laser or the endstop signals. Because it is directly compiled onto the Teensy via the Arduino IDE, it is written in C++.
The rmware supports the following G-Code commands: G0, G1, G2, G3, G28, G60, G61, M3, M4, M5, M201, M203. 8 The rmware sends a short conrmation (usually: OK), when the command is processed. If it included stepper movement (such as G0), the conrmation will only be sent when steppers have reached their target position.

Transmission script The transmission script is a Python script that reads the G-Code le from a specied location on the PC. The gcode is read, encoded and sent via a Serial connection (USB). Before the next line is sent, the script waits for a conrmation from the rmware. This makes sure that no command is sent before the rmware is nished

8For a detailled explanation and syntax details, see the GalvoStep wiki at https://github.com/NiklasHammerstone/GalvoStep

7

processing the previous command. This loop is repeated until no G-Code commands are left to send.

G-Code The G-Code le is a simple text le (.txt) which contains the command lines. It is critical that each line only contains one command.

## 4 Results

4.1 General functionality

The proposed functionality was realised. The prototype can be given commands by sending G-Code commands via the Arduino IDE Serial Monitor or a Python script⁹
. The
commands are executed instantly. No delay between commands is perceivable when a whole G-Code le is executed via the Python script. This results in a smooth movement of the laser spot.
A G-Code le drawing a heart shape was tested with step frequencies of 2000steps
s

up
to 20000steps
s

and a distance from the projection plane of about 200mm. At about 10000 − 12000steps
s

the moving spot started to look like a (more or less) stationary image¹⁰, with the shape of the image still not being noticeably distorted. At about 15000−18000steps
s

the image stationarity was satisfactory, but mechanical vibrations led to a distorted image. The results of this test can be seen in gures 5 and 6. Note that


Figure 5: Arcs of the projected heart at 8000steps
s


Figure 6: Almost entire heart at 20000steps
s

the rolling shutter of the camera is quite fast, which is why only the picture at about 20000steps
s

is (almost) completely visible in one photo. However the dierence of the arcs alone should convey the dience of the whole picture.

9The code les can be downloaded via GitHub: https://github.com/NiklasHammerstone/GalvoStep 10This is only true for the naked eye. Also, the border step frequency is dependent on the size of the image, the background, the laser intensity and the general lighting of the room.

8

4.2 Accuracy and precision


Figure 7: Snapshot of the testing procedure

In order to test the accuracy of the prototype, the following procedure was performed:

1. Place the machine in front of a plane with a dened distance D.
2. Home the mirrors.
3. Move the laser point in 10mm steps in X-, Y-, and XY direction (from -20 to +80) with speed F.¹¹
4. Mark the actual laser spot carefully with a pen for each step (see gure 7)¹²
5. After the testing is done, measure the actual distances of the spots from the origin point.

11An example command for testing the XY direction would be G0 X20 Y20. In this test, X and Y coordinates were always equal to reach an ideal line of slope 1.
12Since the prototype utilizes a 7mW laser diode, the laser itself is too weak to mark the paper by itself.

9

From the Y-, X- and XY, the average and maximum dierence from the ideal coordinates are computed. For the XY-coordinates, average slope and intercept were calculated to analyze the linearity of the system.

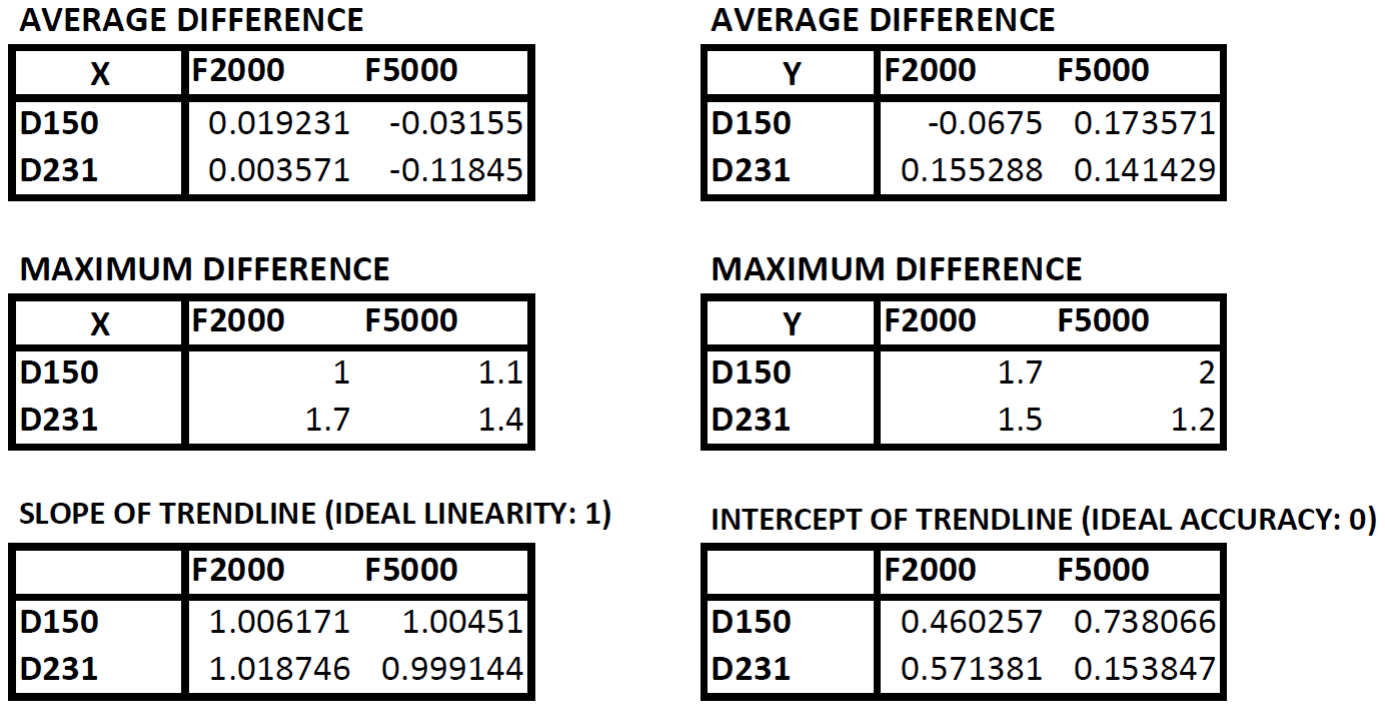
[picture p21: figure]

Figure 8: Results of the accuracy analysis

In gure 8 the results of the mentioned tests are shown. It is expected, that the average and maximum dierences (representing positional accuracy) would rise with rising distance D and feedrate F. However, no such trends can be seen from the data. The average dierence is consistently lower than 0.2mm, but the absolute maximum is 2mm. This suggests relatively high accuracy, but low precision. This is veried by the slope of the trendline for the XY-point testing. The highest dierence from the ideal slope of 1 (since the same values were used for X and Y coordinates simultaneously) was 0.018mm
mm

, suggesting high accuracy. However, the intercepts of the trendlines (ideal would be zero) dier widely from zero, with dierences going as high as 0.738mm, suggesting low precision. This result suggests that the machine is working correctly¹³, but is lacking the mechanical alignment for high precision.
Furthermore, the repeatability of the endstops and backlash of the motors was tested. For the repeatability test of the endstops, the machine was homed ten times (homing speed: 500steps
s

) and the spot osets were noted. The average dierence was about 0.3mm with a maximum of 2mm, resulting in a arc accuracy of 0.5

◦
. These inaccuracies
are most likely due to the cheap mechanical endstops used.
For the backlash test, the machined was homed and the spot was moved by 80mm back

13Working correctlyrefers to the mathematic model being correct and the physical, electrical and optical design being expedient in theory

10 and forth multiple times in X and Y directions. As expected (because no parts are present that could induce backlash), no backlash was perceivable.

4.3 Flaws of the testing methodology

It must be noted that the proposed method of testing has inherent inaccuracies: Since the laser can not mark paper by itself, it is necessary to use a pen, but as soon as the pen is brought into position, it blocks the laser beam. This way its necessary for the operator to visually remember where the spot was. The marked spot can be checked by removing the pen and therefore unblocking the pen, but since both the spot and the pen marking have a diameter of approximately 1.5mm¹⁴, this method can not guarantee results within about half of that range (0.5 − 0.9mm). This can be partly compensated by making sure that the caliper blades are positioned in the exact middle (which itself is only possible within a few tenths of a millimeter) of the pen marking when measuring the points. Also, the paper pieces used for this test did bow out by approximately 1mm, which is unideal. In conclusion, the dierence of laser spot and pen marking and the measuring inaccuracies add up to such a big margin of error (approximately ±1mm) that the exact values of the point coordinates are relatively useless for accuracy analysis. However, since the presented aws are unsystematic and randomn (except for the bow of the paper), the averages (average distance, slope and intercept of trendline) should be more conclusive.
These aws can be elimininated entirely by using a more powerful laser which can mark wood by itself. This would eliminate the pen method with all its aws and inaccuracies and only leave the direct measuring inaccuracies of the calipers, which are usually within 0.02 − 0.1mm.

## 5 Conclusion

In conclusion, the goal of a proof-of-concept for a steppermotor-actuated galvoprojector was reached. The machine can be used via G-Code like a normal CNC-machine (e.g. 3D-printer, CNC-Router) and can draw gures with step speeds of up to 20000steps
s

,
depending on how much distortion is acceptable for the user. Since this machine cannot compete with laser projectors using real galvoactuators, its most probable usecase would be engraving with speeds unreachable for most CO2 or diode daser machines currently on the market. Since the precision of the current prototype is quite limited (as shown in the chaper Results), more work is required to be able compete with normal benchtop laser engravers (see Prospect).

14The actual laser spot is much smaller than this, but appears to be larger due the light being scattered and dispersed in the surrounding paper

11

## 6 Prospect

In the following versions of this machine, the steppermotors and endstops will be upgraded. The base will be re-designed to t the new high-power laser module and the mirrors will be replaced. An F-theta objective might be added to increase light intensity at the working plane and therefore engraving speed. Finally, safety precautions (Enclosure with laser windows and doorswitch) will be added to shield the laser beam. The electronics will not be changed much, since they worked without problems¹⁵

## 7 Acknowledgements

Special thanks to the members of the forum www.laser-engravers.de, especially VDX and Gewindestange, without which a lot more laser diodes would have been destroyed in the process of this project.

## References

[Sem(2007)] NPN − BC368; PNP − BC369 Amplier Transistors. https://www.onsemi.com/pub/Collateral/BC368-D.PDF, 2007.

[lm3(2014)] LM317 - 3-TerminalAdjustableRegulator. https://www.st.com/en/power-management/lm317.html, 2014.

[Meng et al.(2019)Meng, Cao, Li, and Lv] Xianyu Meng, Guohua Cao, Xue Li, and Qiongying Lv. 2-D Scanning Galvanometer Error Analysis and Its Correction. Journal of Physics: Conference Series, 1345:022068, 2019. ISSN 1742-6588. doi: \url{10.1088/1742-6596/1345/2/022068}.

15Maybe a PCB will be designed and manufactured for the schematic.

12

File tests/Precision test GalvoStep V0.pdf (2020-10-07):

AVERAGE DIFFERENCE | AVERAGE DIFFERENCE
X | F2000 | F5000 | Y | F2000 | F5000
D150 | 0.019231 -0.03155 | D150 | -0.0675 0.173571
D231 | 0.003571 -0.11845 | D231 | 0.155288 0.141429
MAXIMUM DIFFERENCE | MAXIMUM DIFFERENCE
X | F2000 | F5000 | Y | F2000 | F5000
D150 | 1 | 1.1 | D150 | 1.7 | 2
D231 | 1.7 | 1.4 | D231 | 1.5 | 1.2
SLOPE OF TRENDLINE (IDEAL LINEARITY: 1) | INTERCEPT OF TRENDLINE (IDEAL ACCURACY: 0)
| F2000 | F5000 | | F2000 | F5000
D150 | 1.006171 | 1.00451 | D150 | 0.460257 0.738066
D231 | 1.018746 0.999144 | D231 | 0.571381 0.153847

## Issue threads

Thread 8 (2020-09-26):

Add ability for teensy to enable/disable steppers

NiklasHammerstone, 2020-09-26:
Connect EN pins to teensy pins with 10k pull-down.

Code: Disable steppers when machine is inactive ( via GCode M17-ON and M18,M84-OFF)

NiklasHammerstone, 2020-09-29:
Not necessary

Closed 2020-09-29.

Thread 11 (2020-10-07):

Update electronics

NiklasHammerstone, 2020-10-07:
Update wiring diagram and prototype report to the final version (for the time being)

NiklasHammerstone, 2020-10-11:
Done!

Closed 2020-10-11.

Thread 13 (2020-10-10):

Perform endstop and backlash tests

NiklasHammerstone, 2020-10-10:
Might be interesting for the reader.

NiklasHammerstone, 2020-10-11:
Done! See prototype report

Closed 2020-10-11.

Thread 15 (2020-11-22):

Modify M6 to specify millis

NiklasHammerstone, 2020-11-22:
currently, M6 is standalone.. Bad..

Haiang, 2021-09-05:
can you edit the Marlin code to include it in the 3D printer's Marlin

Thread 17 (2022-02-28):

ESP32 . support

Haiang, 2022-02-28:
Hi NiklasHammerstone
Can I build on your prototype for ESP32?
And the software that outputs the gcode and is controllable on the ESP32 ?

NiklasHammerstone, 2022-02-28:
Hi Haiang,

feel free to adapt the code to your needs! Unfortunately, I won't be able to help in this matter since I am quite busy at uni.

Haiang, 2022-04-10:
Hi NiklasHammerstone
I thank you for your reply but I have a problem on your build that it can't toggle the Laser with the M3 and M5 commands on the TTL Module. I am using ESP32
Currently I use this laser and this TTL module. If I use a diode laser without TTL driver, it can still turn on and off the M3 and M5 . commands
Secondly, when I use ESP32 and Driver TMC2209, it seems that the X and Y axis moves are not correct even though I have plugged in Jumper JP1 and JP2 to set the step to 1/64 but it still doesn't go correctly.

Haiang, 2022-04-10:
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

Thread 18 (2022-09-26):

X-angle calculation

Linsanity1, 2022-09-26:
Hi Niklas,

Thank you for making this great project open-sourced.
I read the firmware V1 in which I found the x-angle is calculated by
```
angle.x = (atan( x / (E + sqrt(pow(D, 2) + pow(y, 2)) ) ) / 2 ) * 57.2957795131;
```
May I know why the denominator is E + sqrt(pow(D, 2) + pow(y, 2)) ?
Besides, is there any reference for mapping the (x, y) coordinates to motor angles?

NiklasHammerstone, 2022-09-26:
Hi Linsanity1,

the reference I used for mapping the angles to cartesian coordinates [is this one. ](https://iopscience.iop.org/article/10.1088/1742-6596/1345/2/022068)
In this paper, equations for calculating x and y coordinates based on motor angles are given, so I solved them for the angles, resulting in the equation you mentioned.
You can read about it in the Report "Development and construction of a 2D Laser Scanner.pdf", chapter 2.3 in [Documentation](https://github.com/NiklasHammerstone/GalvoStep/tree/master/Documentation)/Prototype report/

I hope this helps!

Nik

Linsanity1, 2022-09-26:
I read the paper and noticed that the calculation is an approximation due to including the term tan(2*theta)*sqrt(d^2+y^2). I guess that using a more detailed model may improve the accuracy/precision (but the authors mainly discussed distortion).
Anyway, thank you very much for replying and the references are definitely helpful!

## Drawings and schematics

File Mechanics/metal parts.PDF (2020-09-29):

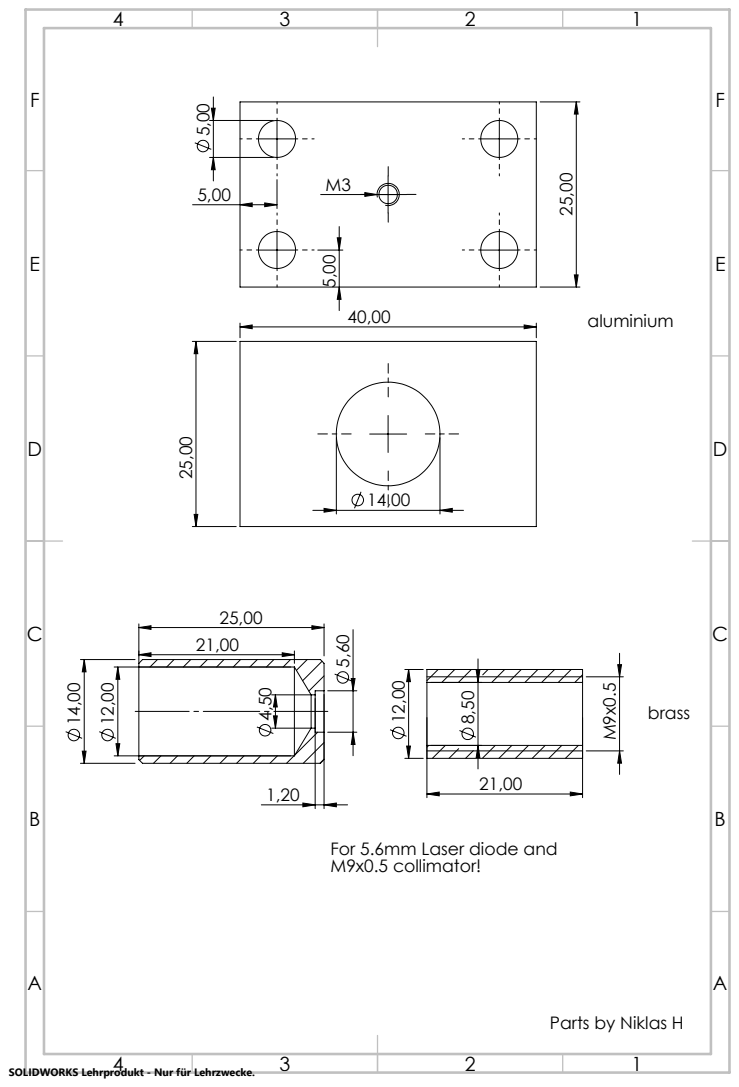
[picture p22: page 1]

For 5.6mm Laser diode and
M9x0.5 collimator!

Parts by Niklas H

SOLIDWORKS Lehrprodukt - Nur für Lehrzwecke.

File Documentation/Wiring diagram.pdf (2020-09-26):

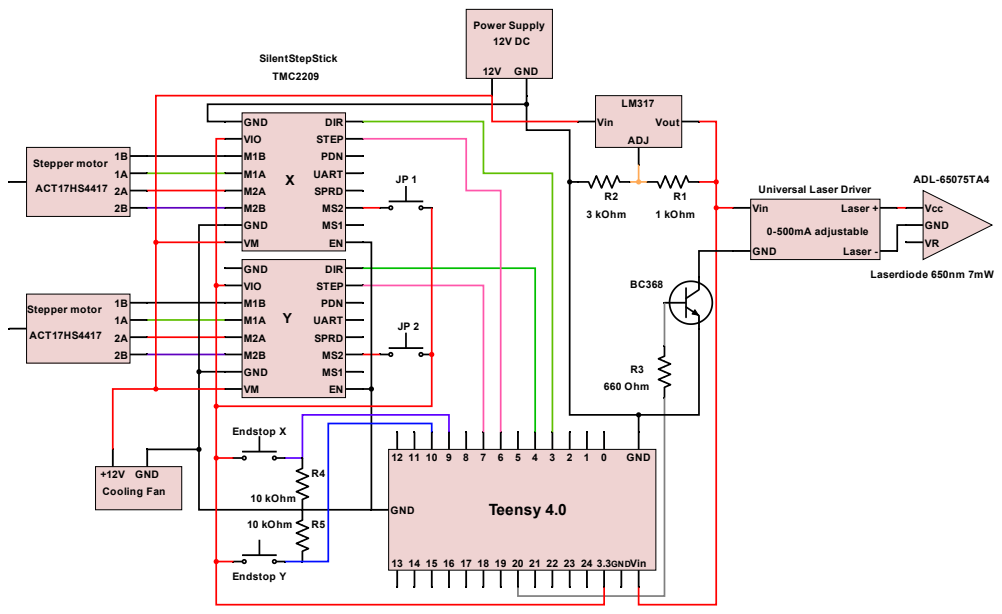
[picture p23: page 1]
Vin; GND; 3.3GND; Teensy 4.0; DIR STEP PDN UART SPRD MS2 MS1; GND VIO; M2B GND; SilentStepStick TMC2209; 12V GND; Power Supply; Stepper motor; ACT17HS4417; 660 Ohm; Vout; ADJ; Vcc; Laserdiode 650nm 7mW; ADL-65075TA4; R1 1 kOhm; R2 3 kOhm; Laser -; Laser +; 0-500mA adjustable; +12V GND Cooling Fan; Endstop X; 10 kOhm; Endstop Y

Universal Laser Driver

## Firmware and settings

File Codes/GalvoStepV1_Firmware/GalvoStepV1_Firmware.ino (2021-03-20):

#include <AccelStepper.h>
#include <MultiStepper.h>

//~~~~~~~~~~ Firmware Settings ~~~~~~~~~~~~

#define D 170 //orthogonal distance of "last" mirror and projection plane
#define E 19  //orthogonal distance of X and Y rotational axes
#define dir_x 3
#define dir_y 4
#define step_x 6
#define step_y 7
#define LASER 14
#define micro_step 64
#define INPUT_SIZE 20  //Maximum length of expected Gcode Commands
#define endswitchX 18
#define endswitchY 20
#define homePosX 1470  //Tweak this to get a perfect 45 deg angle as 0 position
#define homePosY 1350  //Tweak this to get a perfect 45 deg angle as 0 position
#define homeSpeed 1500
#define INTERPOLATION 20    //Radius moves will be approximated by n=INTERPOLATION linear submoves
  
int jogSpeed = 500;   //Default value for G0 jog Speed (step per second)
int workSpeed = 100;  //Default value for G1 work Speed (step per second)

// ~~~~~~~~~~~~~~~~~~~~~~~~~~~~~~~~~~~~~~~~~~~~~~

#define SCB_AIRCR (*(volatile uint32_t *)0xE000ED0C) // Application Interrupt and Reset Control location

  int steps_per_rot = 200*micro_step;
  double degrees_per_step = 360.00 / steps_per_rot;
  struct XY{
    double x;
    double y;
  };

  AccelStepper Xaxis(1, step_x, dir_x); 
  AccelStepper Yaxis(1, step_y, dir_y);

  const byte numChars = INPUT_SIZE;
  char receivedChars[numChars]; // an array to store the received data, max length 20
  boolean newData = false;
  byte workMode = 0;

  struct XY currPos;
  
  struct XY saved;
  
void setup() {

  pinMode(endswitchX, INPUT);
  pinMode(endswitchY, INPUT);
  
  Serial.begin(115200);
  
  pinMode(LASER, OUTPUT);
  pinMode(13, OUTPUT);    //Indicates that the Teensy is working
  digitalWrite(13, HIGH);

  Serial.println("<< GALVO_STEP V1 READY >> ");
}

void loop() {

  recvWithEndMarker();
  if (newData == true){
    readGCode();
    newData = false;}
  if (digitalRead(endswitchY)==HIGH){
    Serial.println("Y has been triggered");
    delay(200);
  }
  if (digitalRead(endswitchX)==HIGH){
    Serial.println("X has been triggered");
    delay(200);
  }

}

void move_To(double x, double y){
  
  struct XY angle;
  angle.y = (atan(y/D) / 2 ) * 57.2957795131 ;
  angle.x = (atan( x / (E + sqrt(pow(D, 2) + pow(y, 2)) ) ) / 2 ) * 57.2957795131 ;
  long step_pos[2];
  step_pos[0] = (long)(angle.x / degrees_per_step);
  step_pos[1] = (long)(angle.y / degrees_per_step);
  MultiStepper steppers;  
  if (workMode == 0){
    Xaxis.setMaxSpeed(jogSpeed);
    Yaxis.setMaxSpeed(jogSpeed);
  }else{
    Xaxis.setMaxSpeed(workSpeed);
    Yaxis.setMaxSpeed(workSpeed);
  }
  steppers.addStepper(Xaxis);
  steppers.addStepper(Yaxis);
  steppers.moveTo(step_pos);
  steppers.runSpeedToPosition();
}

void readGCode(){

  struct XY pos;
  char CommandTypes[]= {'G', 'X', 'Y', 'M', 'I', 'J', 'F'};
  
  double Commands[sizeof(CommandTypes)]={0};
  int CommandIndeces[sizeof(CommandTypes)]={0};

  for (unsigned int j=0;j<sizeof(CommandTypes);j++){
    
    CommandIndeces[j] = indexof(receivedChars, CommandTypes[j]);
    if (CommandIndeces[j] != -1){
      int endIndex = CommandIndeces[j];
      while(receivedChars[endIndex] != ' ' && receivedChars[endIndex] != 0){
        endIndex++;
      }
      endIndex--;
      int dLen =  endIndex - CommandIndeces[j];
      char cmd[dLen+1];
      cmd[dLen]='\0';
      int h = 0;
      for (int k=CommandIndeces[j]+1;k<=endIndex;k++){
        cmd[h] = receivedChars[k];
        h++;
      }
      Commands[j]=atof(cmd);}
  }
  

  if (CommandIndeces[1]!=-1){
      pos.x =  Commands[1];
  }  else{pos.x = currPos.x;}
  
  if (CommandIndeces[2]!=-1){
      pos.y = Commands[2];
  }else{pos.y = currPos.y;}
  
  if(CommandIndeces[0]!=-1){
    switch((int) Commands[0]){
    case 0:
      if (CommandIndeces[6]!=-1){
         jogSpeed = (int) Commands[6];
      } 
      workMode = 0;
      move_To(pos.x, pos.y);
      Serial.println("Moved laser");
      Serial.println("OK");
      break;
    case 1:
      if (CommandIndeces[6]!=-1){
         workSpeed = (int) Commands[6];
      }
      workMode = 1;
      delay(50);
      move_To(pos.x, pos.y);
      delay(10);
      Serial.println("Moved laser");
      Serial.println("OK");
      break;
    case 2:
      if (CommandIndeces[4]==-1){
        Commands[4]=0;}
      if (CommandIndeces[5]==-1){
        Commands[5]=0;}
      moveArc(true, Commands[1], Commands[2], Commands[4], Commands[5]);
      Serial.println("Moved laser");
      Serial.println("OK");
      break;
    case 3:
      if (CommandIndeces[4]==-1){
        Commands[4]=0;}
      if (CommandIndeces[5]==-1){
        Commands[5]=0;}
      moveArc(false, Commands[1], Commands[2], Commands[4], Commands[5]);
      Serial.println("Moved laser");
      Serial.println("OK");
      break;
    case 28:
      homing();
      Serial.println("Mirrors homed successfully.");
      Serial.println("OK");
      break;
    case 60:
      saved.x = currPos.x;
      saved.y = currPos.y;
      Serial.println("Saved the current position");
      Serial.println("OK");
      break;
    case 61:
      pos.x = saved.x;
      pos.y = saved.y;
      move_To(pos.x, pos.y);
      Serial.print("Remembered X:"); Serial.print(pos.x); Serial.print(", Y: "); Serial.println(pos.y);
      Serial.println("OK");
      break;
    case 99:
      Serial.println("RESETTING");
      Serial.end();  //clears the serial monitor  if used
      SCB_AIRCR = 0x05FA0004;  //write value for restart
      break;
    default:
      Serial.println("Command unknown. I'll skip this one.");
      Serial.println("OK");
      break;
  }
  }else{
    switch((int) Commands[3]){
      case 3:
        digitalWrite(LASER, HIGH);
        Serial.println("LASER ON");
        Serial.println("OK");
        break;
      case 4:
        digitalWrite(LASER, HIGH);
        Serial.println("LASER ON");
        Serial.println("OK");
        break;
      case 5:
        digitalWrite(LASER, LOW);
        Serial.println("LASER OFF");
        Serial.println("OK");
        break;
      case 6:
        Serial.println("Firing the Laser for 100ms");
        digitalWrite(LASER, HIGH);
        delay(100);
        digitalWrite(LASER, LOW);
        Serial.println("OK");
        break;
      case 201: //Usage: M201 X[Accel] Y[Accel]      
        Serial.println("Acceleration is deprecated.");
        Serial.println("OK");
      case 203: //Usage: M203 X[maxSpeed] Y[maxSpeed]        
        Serial.println("Max Speed is deprecated.");
        Serial.println("OK");
      break;
    default:
      Serial.println("Command unknown. I'll skip this one.");
      Serial.println("OK");
      break;        
    }
  }
  
  currPos.x = pos.x;
  currPos.y = pos.y;
}

void recvWithEndMarker() {
  //Receives the Command from Serial 
 static byte ndx = 0;
 char endMarker = '\n';
 char rc;

 while (Serial.available() > 0 && newData == false) {
   rc = Serial.read();
   if (rc != endMarker) {
      receivedChars[ndx] = rc;
      ndx++;
   if (ndx >= numChars) {
      ndx = numChars - 1;}
   }
   else {
     receivedChars[ndx] = '\0'; // terminate the string
     ndx = 0;
     newData = true;}
   }
  
}

int indexof(char str[], char c){
  //Returns the index of a char in a chararray. 
  byte j = 0; 
  boolean found = false;
  while(j<numChars){
        if (str[j]!=c){j++; }
        else{found = true; break;}
    }
  if(found){
    return j;}
  else{return -1;}
}

void homing(){

  int prevXmaxSpeed = Xaxis.maxSpeed();
  int prevYmaxSpeed = Yaxis.maxSpeed();
  int prevXspeed = Xaxis.speed();
  int prevYspeed = Yaxis.speed();
  Xaxis.setMaxSpeed(homeSpeed);
  Yaxis.setMaxSpeed(homeSpeed);
  
  Xaxis.setSpeed(-homeSpeed);

  while(digitalRead(endswitchX)==LOW){
    Xaxis.runSpeed();
  }

  Xaxis.setCurrentPosition(0);
  Xaxis.moveTo(homePosX);
  Xaxis.setSpeed(homeSpeed);

  while(Xaxis.distanceToGo() != 0){
    Xaxis.runSpeed();}
  Xaxis.setCurrentPosition(0);

 Yaxis.setSpeed(-homeSpeed);

  while(digitalRead(endswitchY)==LOW){
    Yaxis.runSpeed();
  }

  Yaxis.setCurrentPosition(0);
  Yaxis.moveTo(homePosY);
  Yaxis.setSpeed(homeSpeed);
  while(Yaxis.distanceToGo() != 0){
    Yaxis.runSpeed();}
  Yaxis.setCurrentPosition(0);
  
  Xaxis.setMaxSpeed(prevXmaxSpeed);
  Yaxis.setMaxSpeed(prevYmaxSpeed);
  Xaxis.setSpeed(prevXspeed);
  Yaxis.setSpeed(prevYspeed);
  currPos.x = 0.0;
  currPos.y = 0.0;
}

void moveArc(boolean CW, double X, double Y, double I, double J){
  struct XY center;
  double startAngle;
  double endAngle;
  struct XY startPos = currPos;
  struct XY endPos; endPos.x=X; endPos.y=Y;
  struct XY points[INTERPOLATION];
  double radius = sqrt(pow(I,2)+pow(J,2));
  points[0]=startPos;
  points[INTERPOLATION-1]=endPos;
  
  center.x = startPos.x + I;
  center.y = startPos.y + J;

  startAngle = getAngle(startPos.x-center.x, startPos.y-center.y);
  endAngle = getAngle(endPos.x-center.x, endPos.y-center.y);
  if (CW){
      if(startAngle <= endAngle){
          startAngle += 6.28318530718;
      }
  }else{
    if (startAngle >= endAngle){
      endAngle += 6.28318530718;
    }
  }

  double increment = ((endAngle-startAngle)/(INTERPOLATION-1));
//  Serial.print("Start angle: "); Serial.println(startAngle);
//  Serial.print("End angle: "); Serial.println(endAngle);
//  Serial.print("Angle increment: "); Serial.println(increment);
  double currAngle = startAngle;
  struct XY currPoint;
  for(int i = 1; i<INTERPOLATION-1; i++){
    currAngle += increment;
    currPoint.x = radius*cos(currAngle)+center.x;
    currPoint.y = radius*sin(currAngle)+center.y;
    points[i] = currPoint;
  }
  for(int i=1; i<INTERPOLATION; i++){
    move_To(points[i].x, points[i].y);
    //Serial.print(points[i].x); Serial.print("  "); Serial.println(points[i].y);
  }
}

double getAngle(double x, double y){
  //Retrieves the polar angle phi from a point in cartesian coordinates.
  double phi = atan(y/x);
  if(x >= 0 && y >= 0){
    return phi;
  }else if(x > 0 && y < 0){
    return phi + 6.28318530718;
  }else{
    return phi + 3.14159265359;
  }
}

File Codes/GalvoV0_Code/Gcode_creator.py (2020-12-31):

import cv2
import math
import os



def createGCode(path, x, pixelsize, threshold, feed, jog):
    """Creates Gcode. Uses desired horizontal width (mm) for picture to scale."""

    def calc(val):
        return round(val*pixelsize, 2)

    img = cv2.imread(path, cv2.IMREAD_GRAYSCALE)
    r = img.shape[1]/img.shape[0]
    cv2.imshow("wrench", img)
    columns = math.ceil(x/pixelsize)
    rows = math.ceil(columns * r)
    resized = cv2.resize(img, (columns, rows), interpolation=cv2.INTER_AREA)
    resized = cv2.threshold(resized, threshold, 255, cv2.THRESH_BINARY)[1]
    #cv2.imshow("wrench", img)
    #cv2.imshow("wrench, resized", resized)
    #cv2.waitKey()

    if os.path.exists("laser_gcode.txt"):
        os.remove("laser_gcode.txt")
    f = open("laser_gcode.txt", "w+")
    f.write("G28\r")
    f.write("G0 X0 Y0 F%d\r" % feed)
    laser_on=False
    for i in range(rows):  # y
        prev_val = 255
        if laser_on == True:
            f.write("M5\r")
            laser_on = False
        f.write("G0 X0 Y-{} F{}\r".format(calc(i), jog))
        for j in range(columns):   # x
            if prev_val == 255 and resized[i, j] == 0:
                if j==columns-1:
                    f.write("G0 X{} Y-{} F{}\r".format(calc(j), calc(i), jog))
                    f.write("M6\r")
                elif resized[i,j+1] == 255:
                    f.write("G0 X{} Y-{} F{}\r".format(calc(j), calc(i), jog))
                    f.write("M6\r")
                else:
                    f.write("G0 X{} Y-{} F{}\r".format(calc(j), calc(i), jog))
                    f.write("M3\r")
                    laser_on = True
                prev_val = 0
            elif prev_val == 0 and resized[i, j] == 255:
                f.write("G0 X{} Y-{} F{}\r".format(calc(j-1), calc(i), feed))
                if laser_on == True:
                    f.write("M5\r")
                    laser_on = False
                prev_val = 255
    f.close()


#createGCode("wrench.png", 20, 0.2, 128, 30)

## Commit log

2020-09-26 Added current version of the prototype [NEEDS UPDATIING]
2020-09-26 fixed bug on G61
    [Galvo_firmware.ino]
2020-09-26 updated prototype report
2020-09-26 Created the full wiring diagram
    This should work fine. The laser driver unit depends on your laser.
2020-09-26 Added STL-Files [EXPERIMENTAL]
    [Base part.STL, Endstopholder.STL, Holderclamp.STL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]
2020-09-26 Updated the report to current status
2020-09-29 updated physical build
    [Base part.STL, Base.STL, Endstopholder.STL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]
2020-10-01 Updated speed management in G0, G1, M201 and M203
    speed and accelerations are now in step/s / step/s² but work correctly now.
    [Galvo_firmware.ino]
2020-10-04 Performed a first accuracy analysis
    [Precision test GalvoStep V0.ods]
2020-10-07 performed accuracy analysis of the first prototype
    [Precision test GalvoStep V0.ods]
2020-10-07 small changes to prototype report
2020-10-07 Added picture of prototype
2020-10-10 Added the testing procedure into prototype report
2020-10-11 Finished the prototype report!
    V1, here we come!
2021-01-04 Added current photo
2021-03-20 Speeds and feeds now work correctly
    [GalvoStepV1_Firmware.ino]
